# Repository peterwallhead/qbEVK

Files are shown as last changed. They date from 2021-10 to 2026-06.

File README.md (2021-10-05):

# qbEVK
A modular robotics experiment utilising affordable off-the-shelf components and 3D printing.

## Components

### qbNODE
A 3D printed frame measuring approximately 65x65x60mm holding 4 qbEDGE PCBs, a power supply module and a communications module.

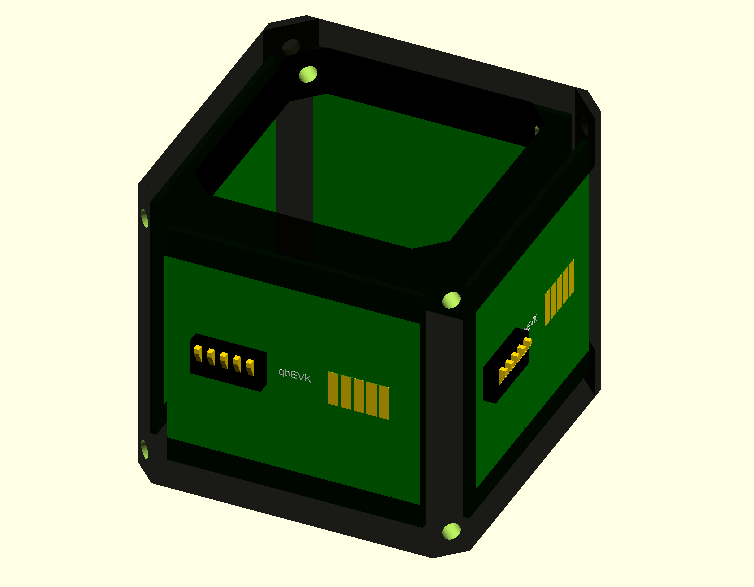
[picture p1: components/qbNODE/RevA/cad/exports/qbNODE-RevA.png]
Exported CAD of RevA qbNODE, excluding power and comms modules


### qbEDGE (RevA in development)
A PCB with its own dedicated ESP32 and power regulation circuit (max power input of 15VDC) which shares a common power rail and RS485 bus with all the edges in the same node. Each edge can be linked to another node using a 5-way spring connector (GND, RS485A, RS485B, I/O, I/O).

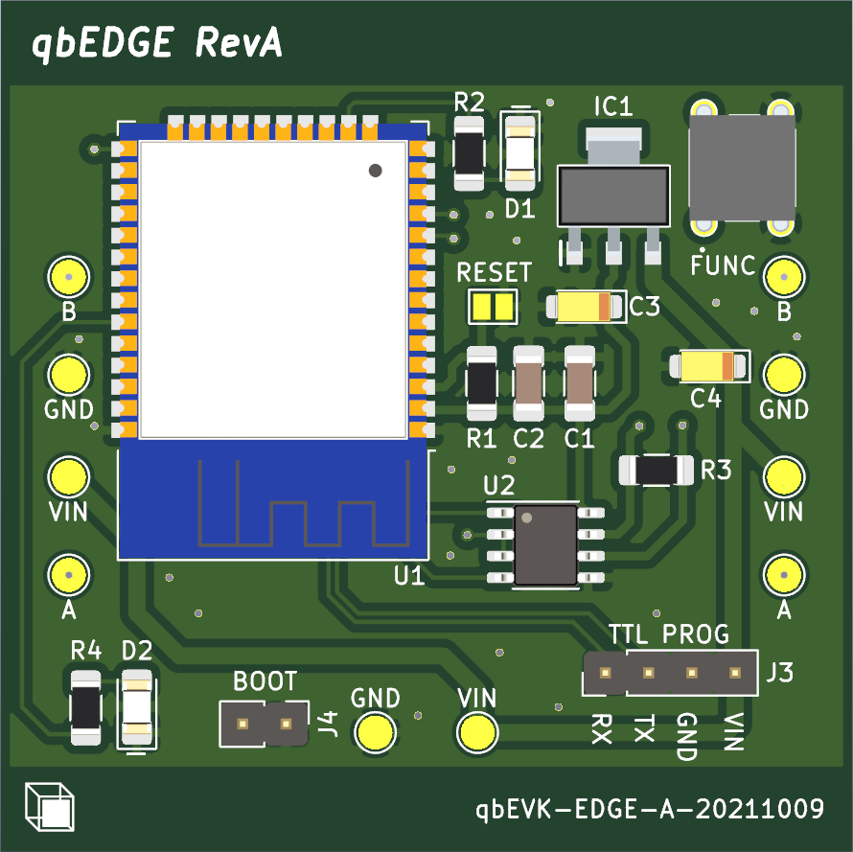
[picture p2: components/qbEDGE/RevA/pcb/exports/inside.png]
qbEDGE RevA PCB - inside

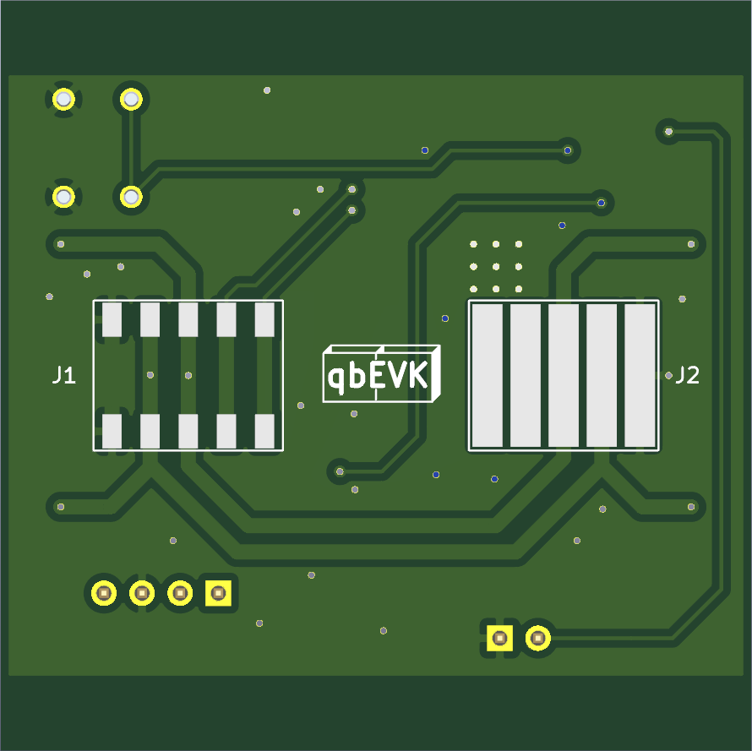
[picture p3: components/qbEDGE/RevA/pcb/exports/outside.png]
qbEDGE RevA PCB - outside


### qbPOWER (Coming soon)
An optional power module mounted in the base of a qbNODE to provide 6-12VDC to each qbEDGE.

### qbCOMMS (Coming soon)
An optional communications module mounted to the top of a qbNODE to interface with the RS485 bus via Serial using an XBee, or other wireless, module.

## Component compatibility
component | compatible with
------------ | -------------
qbNODE RevA | qbEDGE RevA, qbPOWER RevA, qbCOMMS RevA
qbEDGE RevA | qbPOWER RevA, qbCOMMS RevA

## Serial number naming convention
project | component name | revision letter | major.minor.patch numbering (optional) | last revision date
------------ | ------------- | ------------- | ------------- |  -------------
qbEVK | EDGE | A | 1.0.0 | 20211003

***Example:***
```qbEVK-EDGE-A-1.0.0-20211003```

## qbNETWORK
A network comprising of multiple qbNODEs connected together on the same RS485 bus.

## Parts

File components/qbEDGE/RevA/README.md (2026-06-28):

**While the qbEDGE boards were designed to be assembled into qbNODES, you can also use them as standalone ESP32 IO boards running your own code.**

To avoid damaging your ESP32, or other components, please take careful note of the following information during development.

## Pins used
IO | Connected to | Notes
------------ | ------------- | -------------
EN | RESET | Used to reset the board after programming. Pulled to ground when RESET jumper points are bridged
IO0 | BOOT | Used to enable boot mode for programming. Pulled to ground when BOOT header is bridged
TXD0/IO01 | RX on TTL PROG | Used for programming and serial monitoring
RXD0/IO03 | TX on TTL PROG | Used for programming and serial monitoring
IO16 | RO on MAX3485 (U2) | Software Serial RX pin
IO17 | DI on MAX3485 (U2) | Software Serial TX pin
IO18 | RE & DE on MAX3485 (U2) | Serial communication control pin
IO04 | S1 (FUNC) | Pulled to ground (LOW) when FUNC button is pressed
IO13 | D1 | Green LED (Pull HIGH to light LED)
IO21 | D2 | Red LED (Pull HIGH to light LED)
IO26 | Pin 4 on J1 | Read from left to right. Best used as an output pin. Writes to pin 2 on J2 of a connected qbEDGE
IO25 | Pin 5 on J1 | Read from left to right. Best used as an output pin. Writes to pin 1 on J2 of a connected qbEDGE
IO23 | Pin 1 on J2 | Read from left to right. Best used as an input pin. Reads from pin 5 on J1 of a connected qbEDGE
IO22 | Pin 2 on J2 | Read from left to right. Best used as an input pin. Reads from Pin 4 on J1 of a connected qbEDGE

## J1 Connection Guide
__Read from left to right.__
Pin | Connected to | Notes
------------ | ------------- | -------------
1 | GND | Ground
2 | RS485 A | RS485 differential pair A
3 | RS485 B | RS485 differential pair B
4 | IO26 | Best used as an output pin. Writes to pin 2 on J2 of a connected qbEDGE
5 | IO25 | Best used as an output pin. Writes to pin 1 on J2 of a connected qbEDGE

## J2 Connection Guide
__Read from left to right.__
Pin | Connected to | Notes
------------ | ------------- | -------------
1 | IO23 | Best used as an input pin. Reads from pin 5 on J1 of a connected qbEDGE
2 | IO22 | Best used as an input pin. Reads from Pin 4 on J1 of a connected qbEDGE
3 | RS485 B | RS485 differential pair B
4 | RS485 A | RS485 differential pair A
5 | GND | Ground

## Programming quick start

### Parts required
- Assembled qbEDGE board
- 5V compatible USB to TTL converter cable with female jumper ends
- Spare jumper leads
- Optional 2 way jumper cap

### Flash board
*Note: Due to the tight space within an assembled qbNODE, it might be easier to flash your qbEDGEs before final assembly.*

1. Ensure board is not connected to any power source.
2. Connect USB to TTL cable from your computer to the board (RX, TX, GND, VIN).
3. Ensure you can see the board connected to your computer's COM port.
4. Use a jumper cap, or a female to female jumper lead, to bridge the BOOT header.
5. Using a small piece of wire, or a male to male jumper lead, bridge and then release the RESET jumper points on the board to enter programming mode.
6. Flash the board using your preferred IDE or tool chain.
7. Remove the bridge from the BOOT header.
8. Using a small piece of wire, or a male to male jumper lead, bridge and then release the RESET jumper points on the board to exit programming mode.

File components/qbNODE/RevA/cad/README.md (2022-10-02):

# 3D Printing Notes
All tolerances were set for the most accurate print on a specific Flashforge Adventurer 3. Your mileage may vary.

## [end-cap.stl](https://github.com/peterwallhead/qbEVK/blob/master/components/qbNODE/RevA/cad/exports/end-cap.stl)

Designed to be printed with the PCB slots facing upwards.

Print setting | Value
------------ | -------------
Extruder temperature | 200℃
Bed temperature | 60℃
Material | Flashforge Black PLA (test prints)
Infill | 5%
Supports | Yes
Brim | Optional based on printer used
Raft | Optional based on printer used

## [corner-cover.stl](https://github.com/peterwallhead/qbEVK/blob/master/components/qbNODE/RevA/cad/exports/corner-cover.stl)

Designed to printed with the slightly angled sides facing upwards. This piece is decorative as the PCBs should be held tightly in their slots.

Print setting | Value
------------ | -------------
Extruder temperature | 200℃
Bed temperature | 60℃
Material | Flashforge Black PLA (test prints)
Infill | 15%
Supports | No
Brim | Optional based on printer used
Raft | Optional based on printer used

## [jig-clamp.stl](https://github.com/peterwallhead/qbEVK/blob/master/components/qbNODE/RevA/cad/exports/jig-clamp.stl)

Can be used to help keep a qbNODE in place during development and programming by screwing one of theses pieces down to a bench in each corner.

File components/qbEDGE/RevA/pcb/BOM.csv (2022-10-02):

Reference | Quantity | Value | Footprint | Datasheet | Mouser Part Number | Arrow Part Number | Arrow Price/Stock | Description | Height | Manufacturer_Name | Manufacturer_Part_Number | Mouser Price/Stock
C1 | 1 | 100 uF | Capacitor_SMD:C_1206_3216Metric_Pad1.33x1.80mm_HandSolder | ~ | 810-C3216X5R1A107M
C2 | 1 | 1 uF | Capacitor_SMD:C_1206_3216Metric_Pad1.33x1.80mm_HandSolder | ~ | 77-VJ1206Y105MXQRBC
C3 C4 | 2 | 10 uF | Capacitor_Tantalum_SMD:CP_EIA-3216-10_Kemet-I_Pad1.58x1.35mm_HandSolder | ~ | 80-T491A106K016
D1 | 1 | GREEN LED | LED_SMD:LED_1206_3216Metric_Pad1.42x1.75mm_HandSolder | ~ | 710-150120GS75000
D2 | 1 | RED LED | LED_SMD:LED_1206_3216Metric_Pad1.42x1.75mm_HandSolder | ~ | 710-150120SS75000
IC1 | 1 | LT1117IST-3.3#PBF | LT1117IST-3.3#PBF:SOT230P700X180-4N | https://www.analog.com/media/en/technical-documentation/data-sheets/1117fd.pdf | 584-LT1117IST-3.3PBF | LT1117IST-3.3#PBF | https://www.arrow.com/en/products/lt1117ist-3.3pbf/analog-devices | LDO Voltage Regulators 3.3V Low Dropout Regulator | 1.8 | Analog Devices | LT1117IST-3.3#PBF | https://www.mouser.co.uk/ProductDetail/Analog-Devices/LT1117IST-33PBF?qs=ytflclh7QUW4uyPceOhEsg%3D%3D
J1 | 1 | Conn_01x10_Female | Connector_Custom:70AAJ-5-M0G | ~ | 652-70AAJ-5-M0G
J2 | 1 | Conn_01x5_Female | Connector_Custom:70AAJ-5-M0G-MATING-PADS | ~
J3 | 1 | TTL PROG | Connector_PinHeader_2.54mm:PinHeader_1x04_P2.54mm_Vertical | ~
J4 | 1 | BOOT | Connector_PinHeader_2.54mm:PinHeader_1x02_P2.54mm_Vertical | ~
JP1 | 1 | RESET | Jumper:SolderJumper-2_P1.3mm_Open_Pad1.0x1.5mm | ~
R1 | 1 | 10K Ohms | Resistor_SMD:R_1206_3216Metric_Pad1.30x1.75mm_HandSolder | ~ | 652-CR1206JW-103ELF
R2 R4 | 2 | 150 Ohms | Resistor_SMD:R_1206_3216Metric_Pad1.30x1.75mm_HandSolder | ~ | 667-ERJ-8ENF1500V
R3 | 1 | 120 Ohms | Resistor_SMD:R_1206_3216Metric_Pad1.30x1.75mm_HandSolder | ~ | 71-CRCW1206120RFKEAH
S1 | 1 | FUNC | DTS-61N-V:DTS61NV | https://componentsearchengine.com/Datasheets/1/DTS-61N-V.pdf | 113-DTS-61N-V |  |  | Tactile Switches Through Hole 6*6 | 4.3 | Diptronics | DTS-61N-V | https://www.mouser.co.uk/ProductDetail/Diptronics/DTS-61N-V?qs=gTYE2QTfZfTZTPABWXJbEQ%3D%3D
TP1 TP3 TP5 | 3 | VIN | TestPoint:TestPoint_Pad_D2.0mm | ~
TP2 TP4 TP6 | 3 | GND | TestPoint:TestPoint_Pad_D2.0mm | ~
TP7 TP9 | 2 | A | TestPoint:TestPoint_Pad_D2.0mm | ~
TP8 TP10 | 2 | B | TestPoint:TestPoint_Pad_D2.0mm | ~
U1 | 1 | ESP32-WROOM-32 | RF_Module:ESP32-WROOM-32 | https://www.espressif.com/sites/default/files/documentation/esp32-wroom-32d_esp32-wroom-32u_datasheet_en.pdf | 356-ESPWROOM3200US3
U2 | 1 | MAX3485 | Package_SO:SOIC-8_3.9x4.9mm_P1.27mm | https://datasheets.maximintegrated.com/en/ds/MAX3483-MAX3491.pdf | 700-MAX3485ESAT

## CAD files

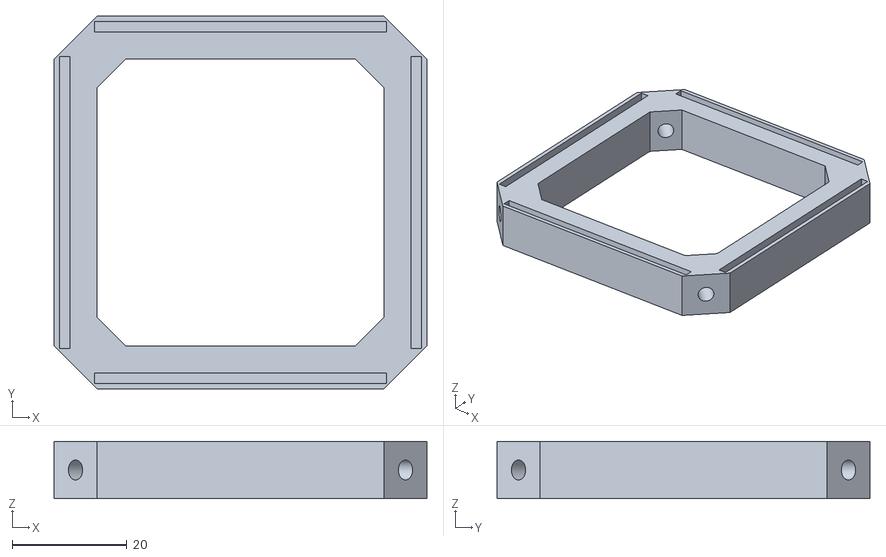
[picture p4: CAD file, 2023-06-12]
components/qbNODE/RevA/cad/exports/end-cap.stl
65.0 x 65.0 x 10.0

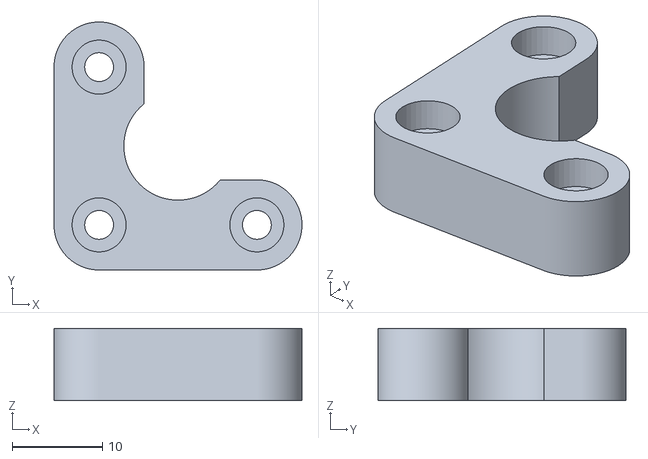
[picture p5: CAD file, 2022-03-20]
components/qbNODE/RevA/cad/exports/jig-clamp.stl
27.5 x 27.5 x 8.00

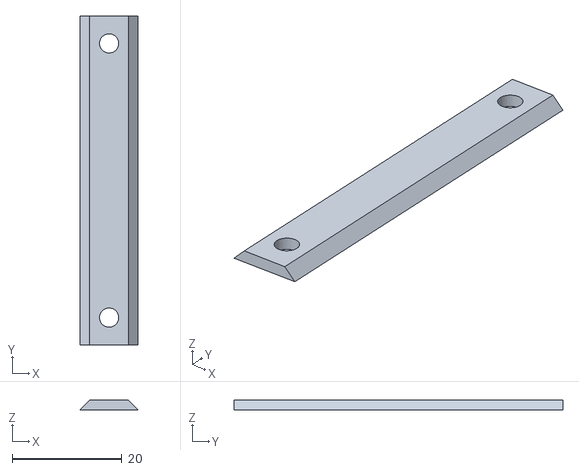
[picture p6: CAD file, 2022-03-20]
components/qbNODE/RevA/cad/exports/corner-cover.stl
10.6 x 60.0 x 1.80

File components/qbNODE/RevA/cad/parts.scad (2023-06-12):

$PCB_THICKNESS = 1.3;
$PCB_COLOUR = "purple";
$SCREEN_PRINT_COLOUR = "white"; 
$FRAME_COLOUR = "lightblue";
$FRAME_COLOUR_TRANSPARENCY = 1;
$CONTACTS = 5;

// All measurements in mm 
$BOLT_DIA = 3;
$BOLT_HOLE_PRINT_TOLERANCE_DIA = 0.5;
$ENDCAP_PCB_LENGTH_TOLERANCE = 0.4;
$STANDOFF_PCB_CUTOUT_TOLERANCE = 0.5;

module pcbSubtraction($pcb_thickness,$thickness_padding,$y_padding) {
    translate([-$thickness_padding/2,-25-$y_padding,-25]) color($FRAME_COLOUR) cube([$pcb_thickness+$thickness_padding,50+($y_padding*2),50]);
}

module pcb($pcb_thickness) {
   translate([0,-25,-25]) color($PCB_COLOUR) cube([$pcb_thickness,50,50]);
   translate([-30,-30.25,0]) rotate([90,0,0]) color($SCREEN_PRINT_COLOUR) linear_extrude(height=1, twist=0) text("qbEVK", size=1.5, halign="center");
   translate([0.31,-2,0]) rotate([90,0,90]) color($SCREEN_PRINT_COLOUR) linear_extrude(1) text("qbEVK", size=1);
}


module cubeCap() {
    difference() {
        translate([0,0,0]) color($FRAME_COLOUR,$FRAME_COLOUR_TRANSPARENCY) linear_extrude(height=10, twist=0)
        polygon(points=[[-25,32.5],[25,32.5],[32.5,25],[32.5,20],[32.5,-20],[32.5,-25],[25,-32.5],[-25,-32.5],[-32.5,-25],[-32.5,-20],[-32.5,20],[-32.5,25]]);
        
        union() {
            translate([0,0,-1]) color($FRAME_COLOUR) linear_extrude(height=12, twist=0)
            polygon(points=[[-20,25],[20,25],[25,20],[25,-20],[20,-25],[-20,-25],[-25,-20],[-25,20]]);
            for (i=[0, 90, 180, 270]) rotate(i) {
                translate([30,0,30]) pcbSubtraction($PCB_THICKNESS,0.5,$ENDCAP_PCB_LENGTH_TOLERANCE);
                translate([-32,32,5]) rotate([90,0,45]) cylinder(d=$BOLT_DIA+$BOLT_HOLE_PRINT_TOLERANCE_DIA,h=15,$fn=36);
            }      
        }    
    }
}

module qbNODE() {
    cubeHardware();
    cubeCornerCovers();
    translate([0,0,60]) rotate([0,180,0]) cubeCap(); // top
    cubeCap(); // bottom   
}

module cubeCornerCover() {
    difference() {
        translate([-25,32.5,0]) color($FRAME_COLOUR,$FRAME_COLOUR_TRANSPARENCY) linear_extrude(height=60, twist=0)
        polygon(points=[[0,0],[-2.5,0],[-7.5,-5],[-7.5,-7.55]]);
        
        union() {
            translate([-32,32,5]) rotate([90,0,45]) cylinder(d=$BOLT_DIA+$BOLT_HOLE_PRINT_TOLERANCE_DIA,h=15,$fn=36);
            translate([-32,32,55]) rotate([90,0,45]) cylinder(d=$BOLT_DIA+$BOLT_HOLE_PRINT_TOLERANCE_DIA,h=15,$fn=36);
        }
    }
}

module cubeCornerCovers() {
    for (i=[0,90,180,270]) rotate(i) {
        cubeCornerCover();
    }
}

module cubeHardware() {
    for (i=[0, 90, 180, 270]) rotate(i) {
        translate([30,0,30]) pcb($PCB_THICKNESS);
        translate([31.2,-12.5,30]) mountingContacts($CONTACTS);
        translate([31.2,12.5,30]) mountingPads($CONTACTS);
    }
}

module mountingPads($pins) {
    // All measurements are approximate. Consider this an analog, not a realistic model
    translate([0,-(($pins*2.5)/2)+.25,-3.5]) union() {
        for (i=[0:$pins-1])  {
            color("gold") translate([0.02,i*(0.5+2),0]) cube([0.1,2,7]);
        }
        color($PCB_COLOUR) translate([0.01,-.25,0]) cube([0.1,$pins*2.5,7]);
    }
}

module mountingContacts($pins) {
    // All measurements are approximate. Consider this an analog, not a realistic model
    translate([0,0,3.5]) union() {
        translate([2.54,-0.5+((($pins-1)/2)*2.54),0])
        for (i=[0:$pins-1])  {
            translate([0,-(i*(2.54)),0]) rotate([0,-90,-90]) color("gold") linear_extrude(height=1, twist=0) polygon(points=[[0,0],[-3.5,0],[-1,1.27],[0,1.27]]);
        }
        color("black") translate([0,-($pins*2.77)/2,-6.5]) cube([2.54,$pins*2.77,7]);
    }
}

module jigClamp() {
    color("white") difference() {
        union() {
            translate([0,0,0]) linear_extrude(height=8, twist=0)
                polygon(points=[[5,0],[12.5,0],[12.5,-10],[-5,-10],[-10,-5],[-10,12.5],[0,12.5],[0,5]]);

            translate([12.5,-5,0]) cylinder(d=10,h=8,$fn=360);
            translate([-5,12.5,0]) cylinder(d=10,h=8,$fn=360);
            translate([-5,-5,0]) cylinder(d=10,h=8,$fn=360);
        }
        
        union() {
            //Bolt holes
            translate([12.5,-5,-1]) cylinder(d=3.2,h=10,$fn=36);
            translate([-5,12.5,-1]) cylinder(d=3.2,h=10,$fn=36);
            translate([-5,-5,-1]) cylinder(d=3.2,h=10,$fn=36);
            
            //Countersinks
            translate([12.5,-5,5]) cylinder(d=6,h=5,$fn=36);
            translate([-5,12.5,5]) cylinder(d=6,h=5,$fn=36);
            translate([-5,-5,5]) cylinder(d=6,h=5,$fn=36);
            translate([3.75,3.75,-1]) cylinder(d=12,h=10,$fn=360);
            
        }
    }
    
    
}

// Uncomment to render mockup images of complete node
qbNODE();
//translate([70,0,0]) qbNODE();
//translate([70,70,0]) qbNODE();
//translate([0,70,0]) qbNODE();

// Uncomment to generate STL exports
//translate([0,25,-40]) rotate([90,45,0]) cubeCornerCover();
//cubeCap();
//jigClamp();

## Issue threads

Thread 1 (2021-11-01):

Reduce PCB slot tolerance

peterwallhead, 2021-11-01:
The PCB slot in the end caps of the qbNODE currently have a 1mm tolerance in length. As discovered in the first print of this piece, this allows the qbEDGE PCB to slide left and right too far.

Closed 2021-11-01.

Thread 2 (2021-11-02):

Corner pillar standoffs collide with PCB

peterwallhead, 2021-11-02:
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

May need to reduce the standoff diameter slightly, or adjust its profile.

Closed 2021-11-02.

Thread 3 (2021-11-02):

Corner pillar standoff embedded nuts

peterwallhead, 2021-11-02:
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

Are not seating fully, and are hard to insert. Need to increase the tolerances.

Closed 2021-11-02.

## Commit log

2021-10-02 Adds exported cad for README
2021-10-02 Adds qbNODE RevA OpenSCAD design
    [parts.scad]
2021-10-03 Adds colour variables
    [parts.scad]
2021-10-03 Adds RevA STLs
    [corner-pillar.stl, end-cap.stl]
2021-10-05 Adds RevA PCB images
2021-10-05 Adds first PCB images
2021-10-06 Added bolt hole dimension variables
    [parts.scad]
2021-10-09 Updates first print run PCB design
2021-10-24 Adds support for transparency of frame when rendering
    [parts.scad]
2021-11-01 Adds embedded nut slots to simplify frame construction
    [corner-pillar.stl, parts.scad]
2021-11-01 Corrects bolt hole sizes
    [corner-pillar.stl, parts.scad]
2021-11-01 Fixes #1
    [end-cap.stl, parts.scad]
2021-11-01 Adds initial 3D printing notes
2021-11-02 Fixes #2, fixes #3
    [corner-pillar.stl, end-cap.stl, parts.scad]
2021-11-02 Defaults rendered 3D view
    [parts.scad]
2021-11-02 Updates print settings
2022-03-20 Updates CAD model to latest working version
    [corner-pillar.stl, end-cap.stl, parts.scad]
2022-03-20 Adds jig clamp model
    [jig-clamp.stl, parts.scad]
2022-10-02 Adds RevA Gerber files and BOM
    [BOM.csv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]
2022-10-02 Updates part naming and print settings
    [corner-cover.stl, parts.scad]
2023-06-12 Increases 3D printing tolerances
    [end-cap.stl, parts.scad]
2026-06-28 Add additional spring connector usage guides
